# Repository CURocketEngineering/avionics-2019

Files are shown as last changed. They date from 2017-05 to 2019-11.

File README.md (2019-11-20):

## Deprecated
For more information, visit the [new, Python implementation](https://github.com/CURocketEngineering/avionics_main).

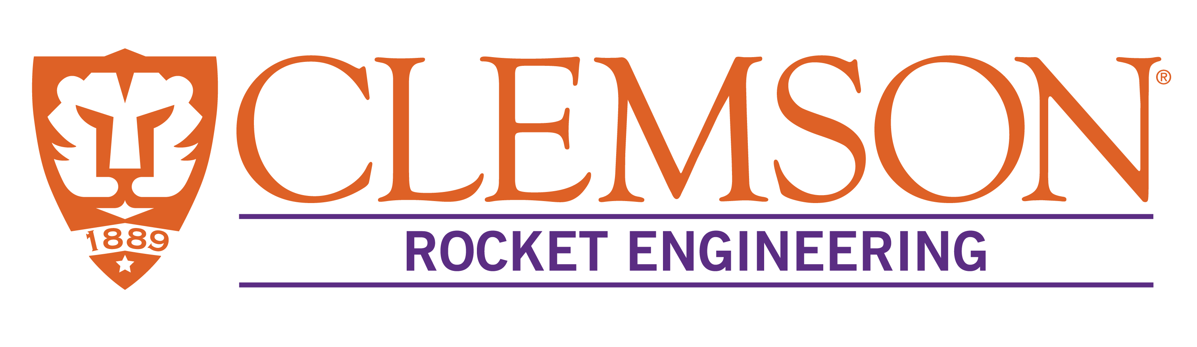
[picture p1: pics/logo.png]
CURocket Logo


### About
Clemson University Rocket Engineering (CURE) Avionics subteam program files. 
Powers CURE's competitive and non-competitive rockets. Used in the 
Intercollegiate Rocket Engineering Competition. Begun by Foster McLane, 2016.

### Documentation
* [`base/`](base/)
  * Code ran on the CURE base station for communication and telemetry
  * `main.py` for basic communication
  * `mpl.py` for graphical interpretation
  * `mpl_simulator.py` for simulating graphical interpretation
* [`cad/`](/cad)
  * Files for electrically engineering components in `eagle`
* [`data/`](data/)
  * Flight data
  * `jsongrapher.py` for ensuring simulation (and actual) data 
  * ['Complete simulation'](data/sim_data_graphed) for pictures of complete simulations
* [`extra/`](extra/)
  * Testing
  * GPS and XBEE `.ino` files
* [`main/`](main/)
  * Code ran on CURE rockets used for data collection, state changes, and telemetry
* [`pics/`](pics/)
  * Pictures used in this github
* [`xbee/bypass/`](xbee/bypass/)
  * Communication

### License
This project is licensed used the GNU General Public License v3.0

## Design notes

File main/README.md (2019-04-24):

# On-board avionics
### Usage
#### Compiling and Running
1. `make` to compile and run
#### Debugging
1. *todo*
#### Configuration
Configuration for several parameters can be made via `config.h`.

### Components
#### Current Components
* General Hardware
  * Teensy 3.5 Arduino
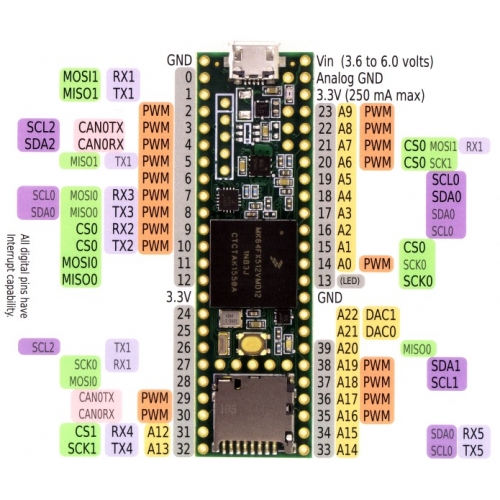
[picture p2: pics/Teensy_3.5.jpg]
Teensy
  * 
* Sensors
  1. 9DOF - 3D gyroscope, magnetometer, and accelerometer
     * [sparkfun link](https://www.sparkfun.com/products/13944)
       * schematic and eagle files provided
     * I2C interface
  2. BME280 - altitude, pressure, and temperature
     * [sparkfun link](https://www.sparkfun.com/products/13676)
       * schematic and eagle files provided
     * 3.3V SPI interface and 5V tolerant I2C
     * 10 pins, < 6 used
  3. GPS 

### Wishlist
1. XBEE Voice Messages
2. Live video feed

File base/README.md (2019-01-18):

# Base Telemetry
### TODO
* Write `graph/` functions
  * speedometer
  * pitch, yaw, roll
* `mpl.py` aesthetic
* Where is command located in main?
* Command integration in mpl
* Camera?

### Running
#### Compiling and Running
1. `python2 main.py` for main telemetry
2. `python3 mpl.py` for visual data
   * Requires `main.py` to be running
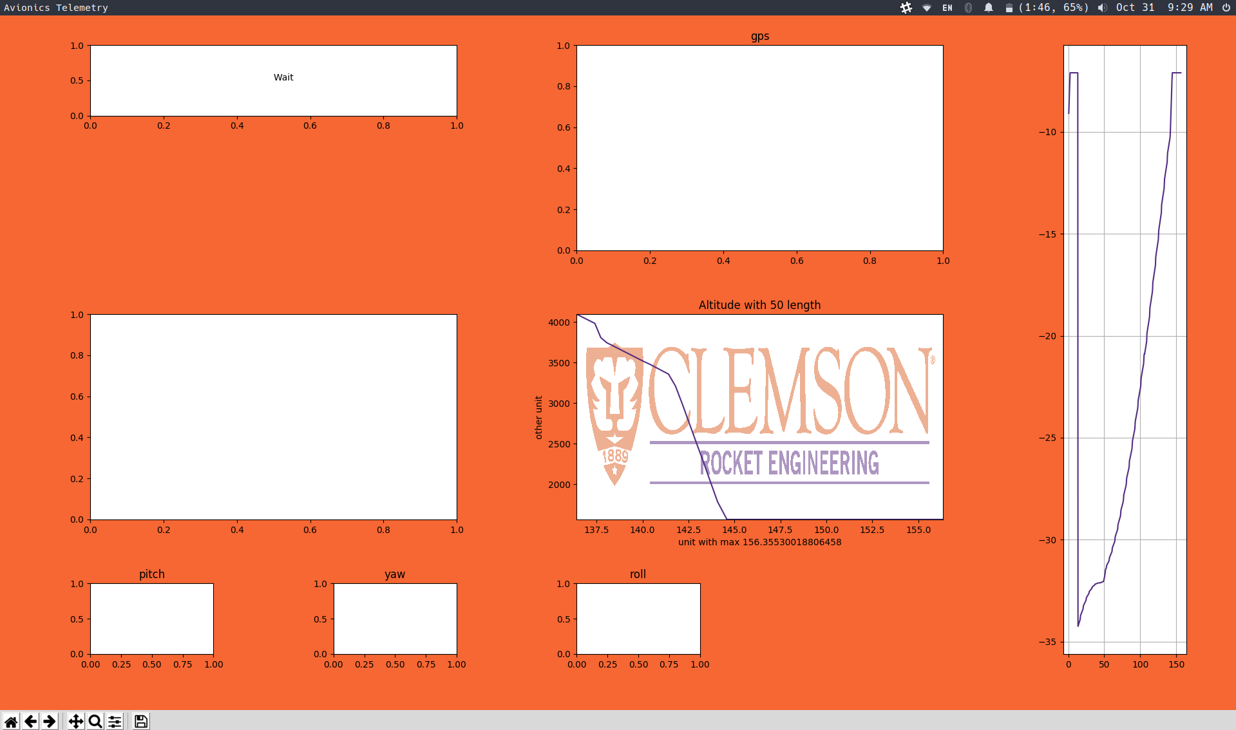
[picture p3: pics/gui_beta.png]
gui
   
#### Debugging
* To debug and test `mpl.py`
  1. Run `python3 mpl_simulator.py`
  2. Also run `python3 mpl.py` while the other is running
  3. Look at graphs and adjust program
* To debug and test `main.py`
  1. Pray to ~~the gods~~Foster that it works

### Information
* JSON Formatting
  * example: `{"sensors":{"gyro":{"x":0,"y":0,"z":0},"acc":{"x":0.000025,"y":0.000025,"z":38.01759},"mag":{"x":0,"y":0,"z":0},"att":{"r":6.451225e-7,"p":-6.451225e-7,"y":-0.108385},"bar":{"p":101324.9,"dp":0.890625,"alt":0.001904,"gnd":1237.593,"temp":0,"hum":0},"gps":{"lat":0,"lon":0,"hour":0,"min":0,"sec":0,"day":0,"mon":0,"year":0}},"type":"telemetry","time":804}`
  * Rocket will return self-contained json
    * Will always contain `type`, `time`, and `state`
      * `type` will be 1 of: state, telemetry, 
      * `time` is in units of (ms?)...
      * `state` will be 1 of the states: ignite, burn, apogee, wait, eject, fall, recover
    * Telemetry contains ... TODO

### Components
#### Current Components
* Communications Antenna
  * ???

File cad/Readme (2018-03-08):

Sparkfun Names of sensors (in eagle "add" component):
   1. Venus GPS ->                   GPS/ VENUS638FLPX-L
   2. Atmospheric Sensor Breakout -> Sensors/ BME280
   3. 9DoF Sensor Stick ->           Sensors/ LSM9DS1
   4. Antenna ->                     RF/ XBEE

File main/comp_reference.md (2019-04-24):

# Component Size Reference
### Summer 2019
| Component  | Length | Width | Iregular | Height |
| :--- | --- | --- | --- | --- |
| Teensy 3.6 | 2.5 in | 1.75 in | false | 1.3 in |
| 9Dof | 0.9 in | 0.25 in | false | |
| BME280 | 0.9 in | 0.5 in  | false | |
| | | | | |
| Antenna | 7 in | | diameter = 0.25 in | |

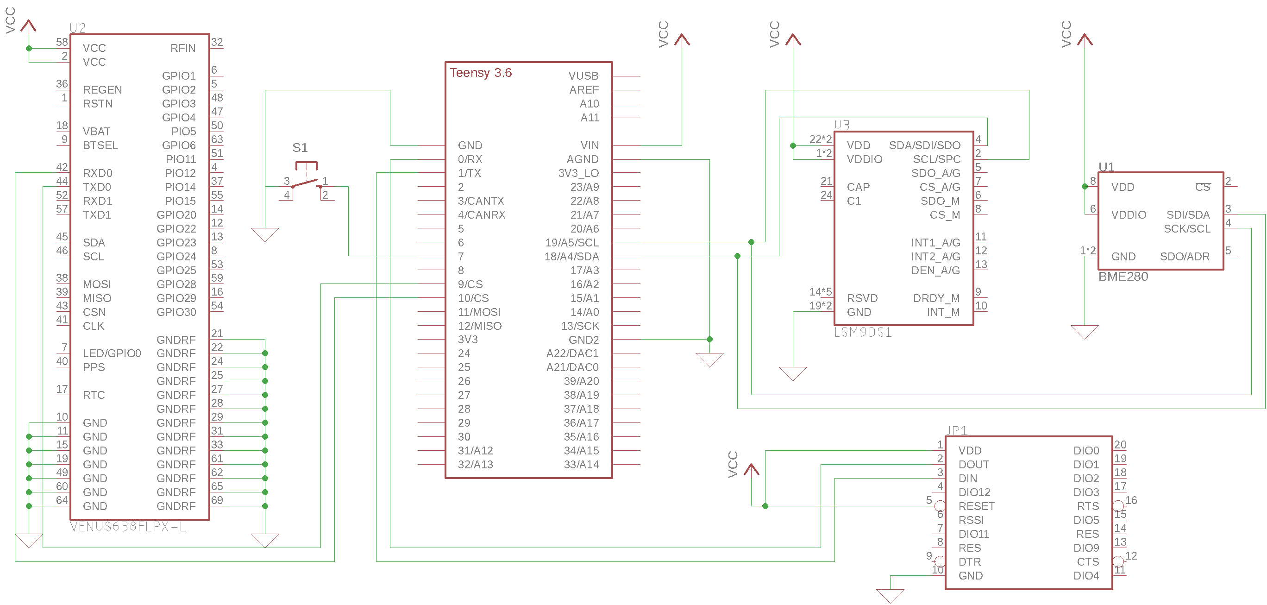
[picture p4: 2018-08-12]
cad/avionics-schematic.png

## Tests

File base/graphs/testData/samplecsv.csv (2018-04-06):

Time (sec) | Stage | Stage Time (sec) | Mach Number | Angle of Attack (deg) | CD | CL | Thrust (lb) | Weight (lb) | Drag (lb) | Lift (lb) | CG (in) | CP (in) | Stability Margin (cal) | Accel (ft/sec^2) | Accel-V (ft/sec^2) | Accel-H (ft/sec^2) | Velocity (ft/sec) | Vel-V (ft/sec) | Vel-H (ft/sec) | Pitch Attitude (deg) | Flight Path Angle (deg) | Altitude (ft) | Distance (ft) | Pressure (Pa)
0.010 | S | 0.010 | 0.010 | 0 | 0.5009655 | 0 | 152.8668 | 70 | 0 | 0 | 72.31744 | 79.27036 | 1.158819 | 38.0879567091562 | 38.0879567089588 | 0.000122630241795288 | 0.380879600001974 | 0.3808796 | 0.000001226302 | 89.9999 | 89.9999 | 0.001904398 | 0.00000000613151 | 101324.99
0.02 | S | 0.02 | 0.010 | 0 | 0.5009655 | 0 | 284.6732 | 69.99571 | 0.00001369519 | 0 | 72.30488 | 79.27036 | 1.160913 | 98.6779204506105 | 98.6779204503462 | 0.000228379674998849 | 1.3676590000045 | 1.367659 | 0.000003510099 | 89.9999 | 89.9999 | 0.01064709 | 0.00000002981351 | 101324.96
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

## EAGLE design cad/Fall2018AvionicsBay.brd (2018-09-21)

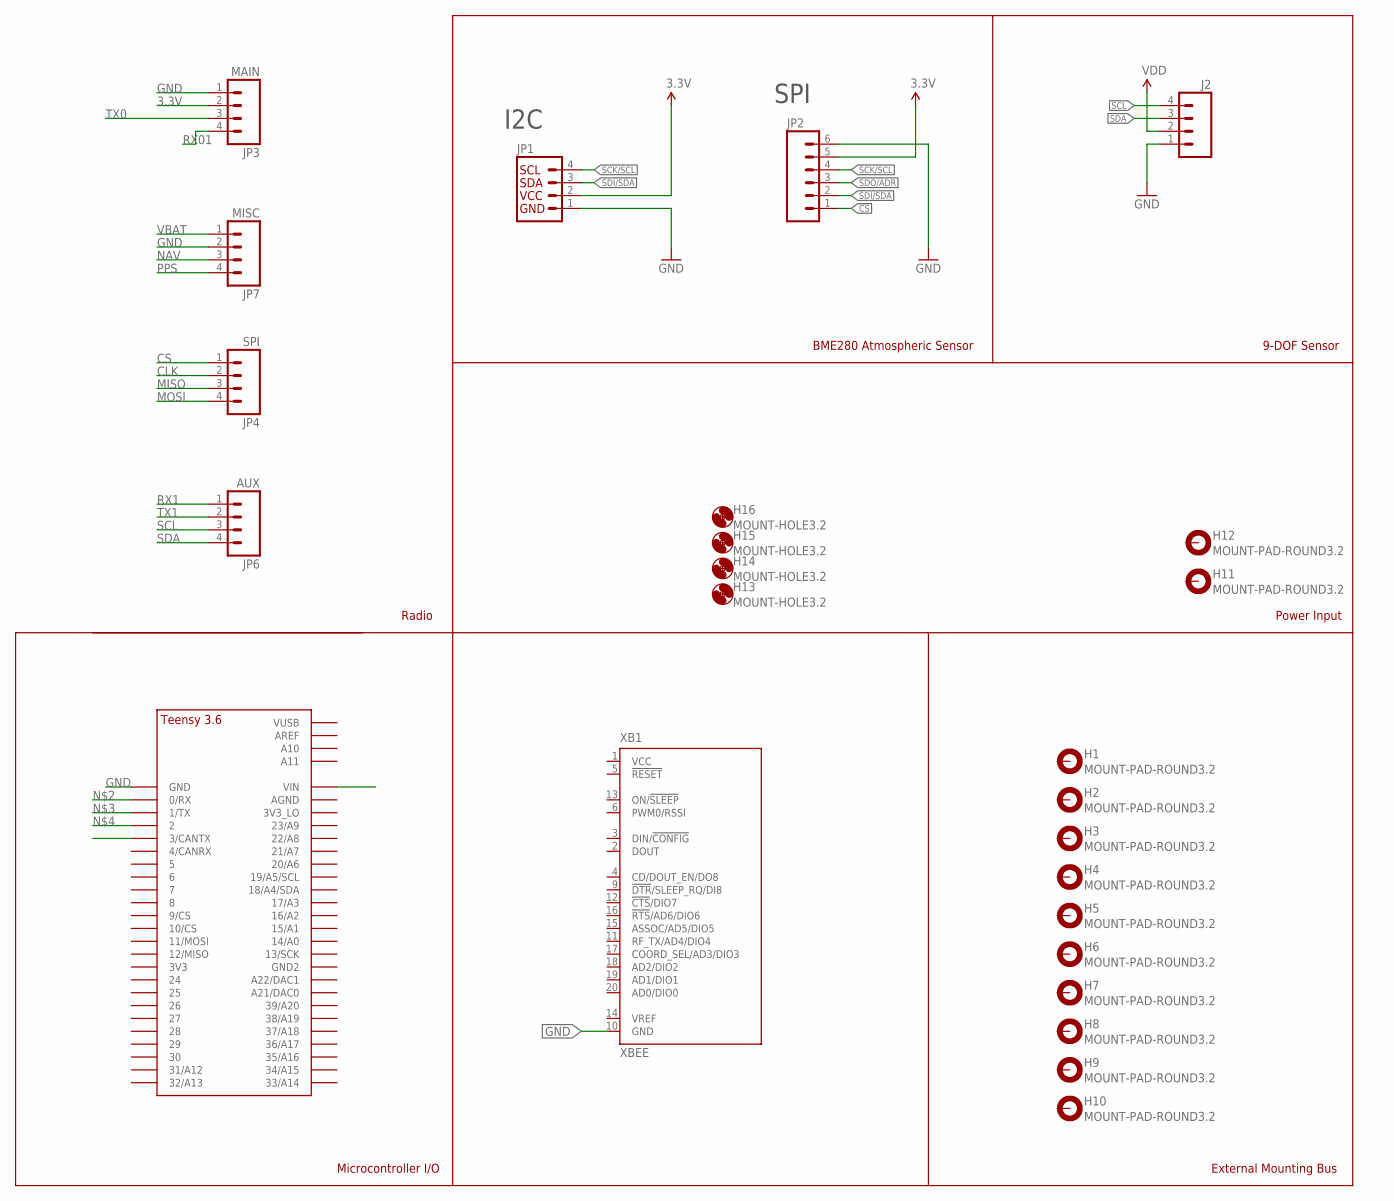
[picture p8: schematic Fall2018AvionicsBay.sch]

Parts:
H1, H2, H3, H4, H5, H6, H7, H8, H9, H10, H11, H12: MOUNT-PAD-ROUND3.2; 3,2-PAD
H13, H14, H15, H16: MOUNT-HOLE3.2; 3,2
J2: M04NO_SILK_ALL_ROUND; 1X04_NO_SILK_ALL_ROUND
JP1: I2C_STANDARD_NO_SILK; 1X04_NO_SILK
JP2: M06NO_SILK_FEMALE_PTH; 1X06_NO_SILK
JP3: MAIN; 1X04
JP4: SPI; 1X04
JP6: AUX; 1X04
JP7: MISC; 1X04
U$1: TEENSY_3.5/3.6_BASIC
XB1: XBEE

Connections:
3.3V: JP1.2, JP2.5, JP3.2
!CS: JP2.1
CLK: JP4.2
CS: JP4.1
GND: J2.1, JP1.1, JP2.6, JP3.1, JP7.2, U$1.GND, XB1.10 (GND)
MISO: JP4.3
MOSI: JP4.4
NAV: JP7.3
PPS: JP7.4
RX1: JP6.1
RX01: JP3.4
SCK/SCL: JP1.4, JP2.4
SCL: J2.4, JP6.3
SDA: J2.3, JP6.4
SDI/SDA: JP1.3, JP2.2
SDO/ADR: JP2.3
TX0: JP3.3
TX1: JP6.2
VBAT: JP7.1
VCC: XB1.1 (VCC)
VDD: J2.2

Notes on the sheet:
Microcontroller I/O
Radio
9-DOF Sensor
I2C
SPI
BME280 Atmospheric Sensor
External Mounting Bus
Power Input

Board: 2 copper layers, 25 parts (4 on the bottom side), 6 nets, no tracks yet.

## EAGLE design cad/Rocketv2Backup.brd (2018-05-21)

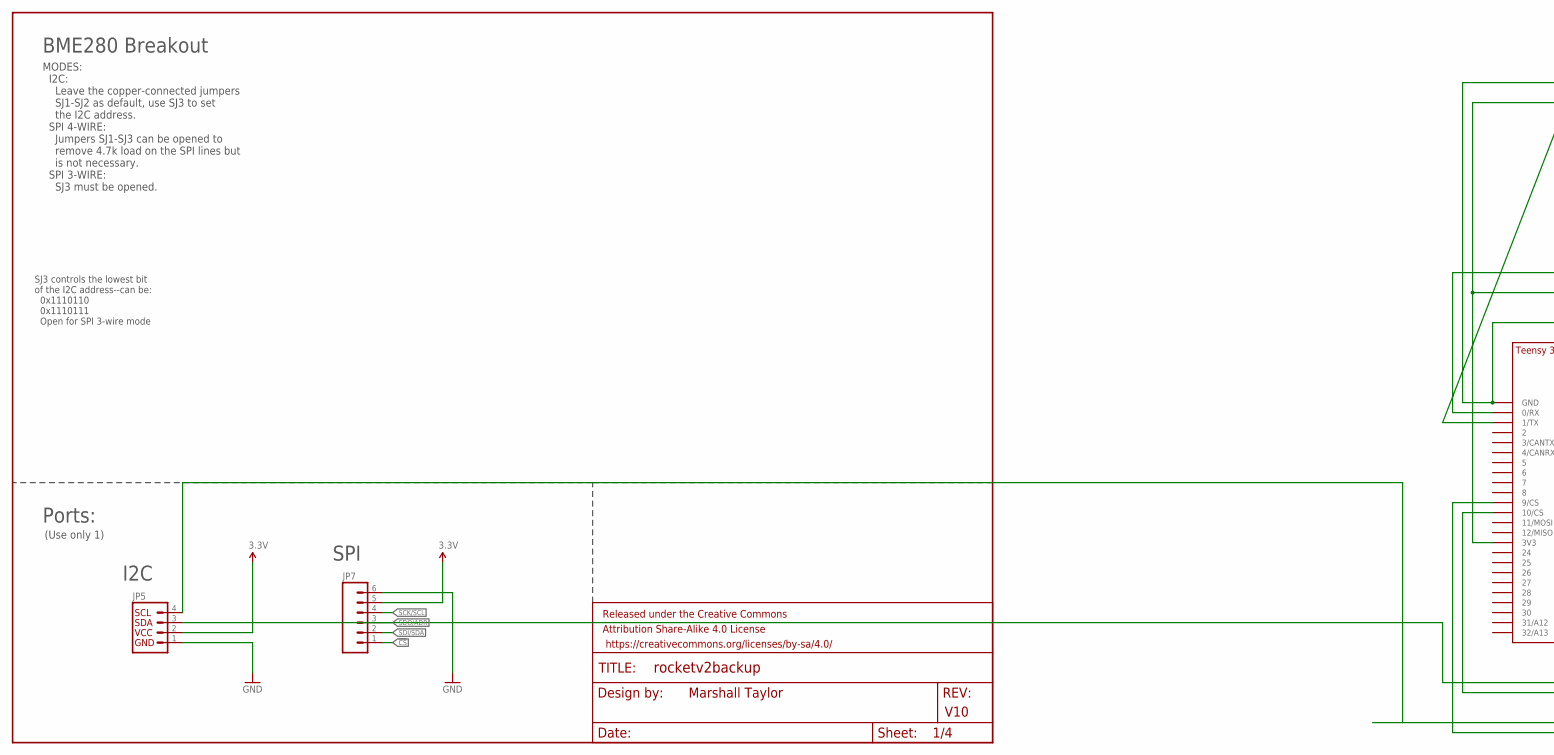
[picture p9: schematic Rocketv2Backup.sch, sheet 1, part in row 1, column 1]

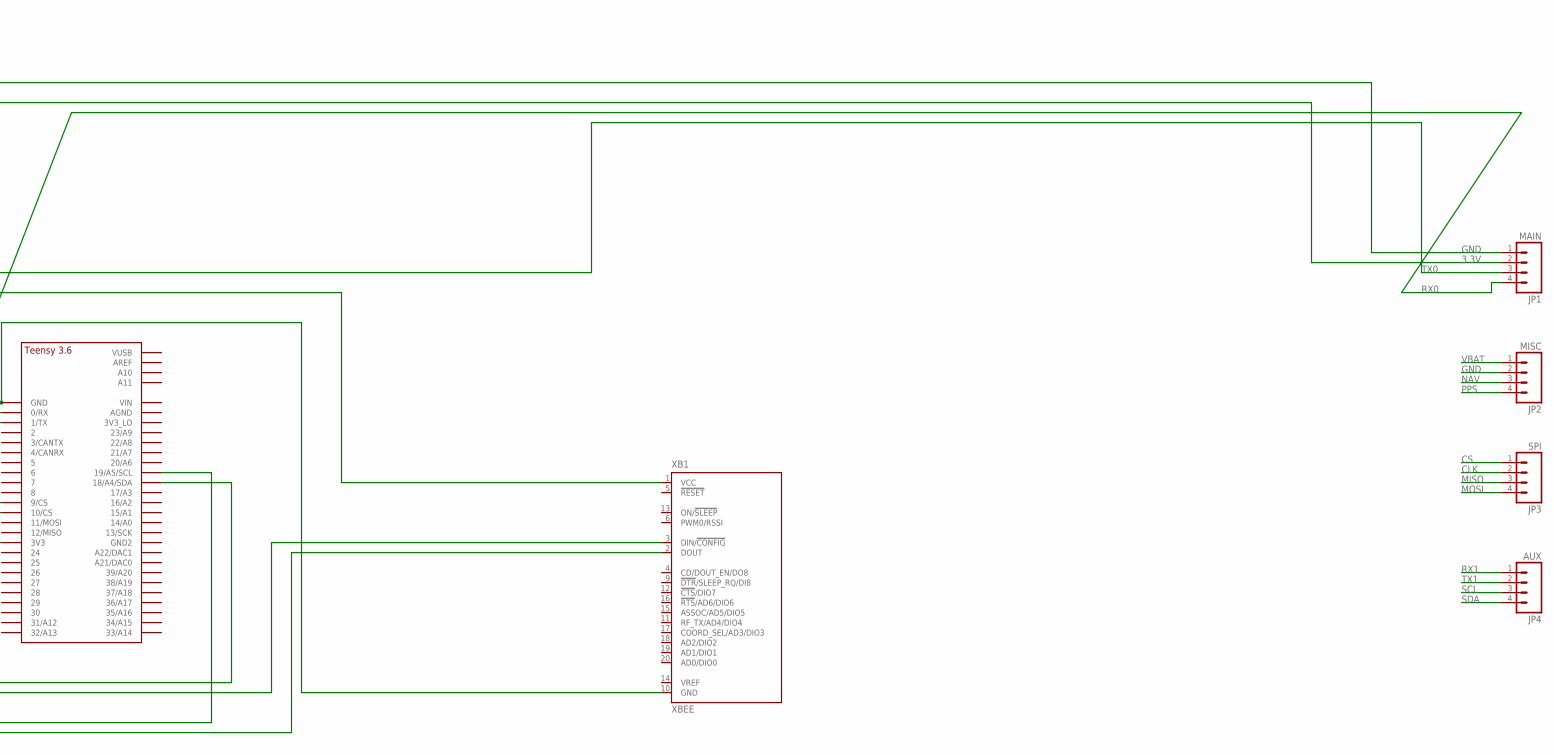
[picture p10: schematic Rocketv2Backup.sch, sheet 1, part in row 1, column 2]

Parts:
FRAME3: FRAME-LETTER; CREATIVE_COMMONS
JP1: MAIN; 1X04
JP2: MISC; 1X04
JP3: SPI; 1X04
JP4: AUX; 1X04
JP5: I2C_STANDARD_NO_SILK; 1X04_NO_SILK
JP7: M06NO_SILK_FEMALE_PTH; 1X06_NO_SILK
U$1: TEENSY_3.5/3.6_BASIC
XB1: XBEE

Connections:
3.3V: JP1.2, JP5.2, JP7.5, U$1.3V3, XB1.1 (VCC)
!CS: JP7.1
CLK: JP3.2
CS: JP3.1
GND: JP1.1, JP2.2, JP5.1, JP7.6, U$1.GND, XB1.10 (GND); also elsewhere on the board
MISO: JP3.3
MOSI: JP3.4
unnamed: JP5.4, U$1.19/A5/SCL
unnamed: U$1.10/CS, XB1.3 (DIN/!CONFIG)
unnamed: U$1.9/CS, XB1.2 (DOUT)
NAV: JP2.3
PPS: JP2.4
RX0: JP1.4, U$1.1/TX
RX1: JP4.1
SCK/SCL: JP7.4
SCL: JP4.3; also elsewhere on the board
SDA: JP4.4; also elsewhere on the board
SDI/SDA: JP5.3, JP7.2, U$1.18/A4/SDA
SDO/ADR: JP7.3
TX0: JP1.3, U$1.0/RX
TX1: JP4.2
VBAT: JP2.1

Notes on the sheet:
Marshall Taylor
V10
BME280 Breakout
SJ3 controls the lowest bit of the I2C address--can be: 0x1110110 0x1110111 Open for SPI 3-wire mode
Ports:
(Use only 1)
I2C
SPI
MODES: I2C: Leave the copper-connected jumpers SJ1-SJ2 as default, use SJ3 to set the I2C address. SPI 4-WIRE: Jumpers SJ1-SJ3 can be opened to remove 4.7k load on the SPI lines but is not necessary. SPI 3-WIRE: SJ3 must be opened.

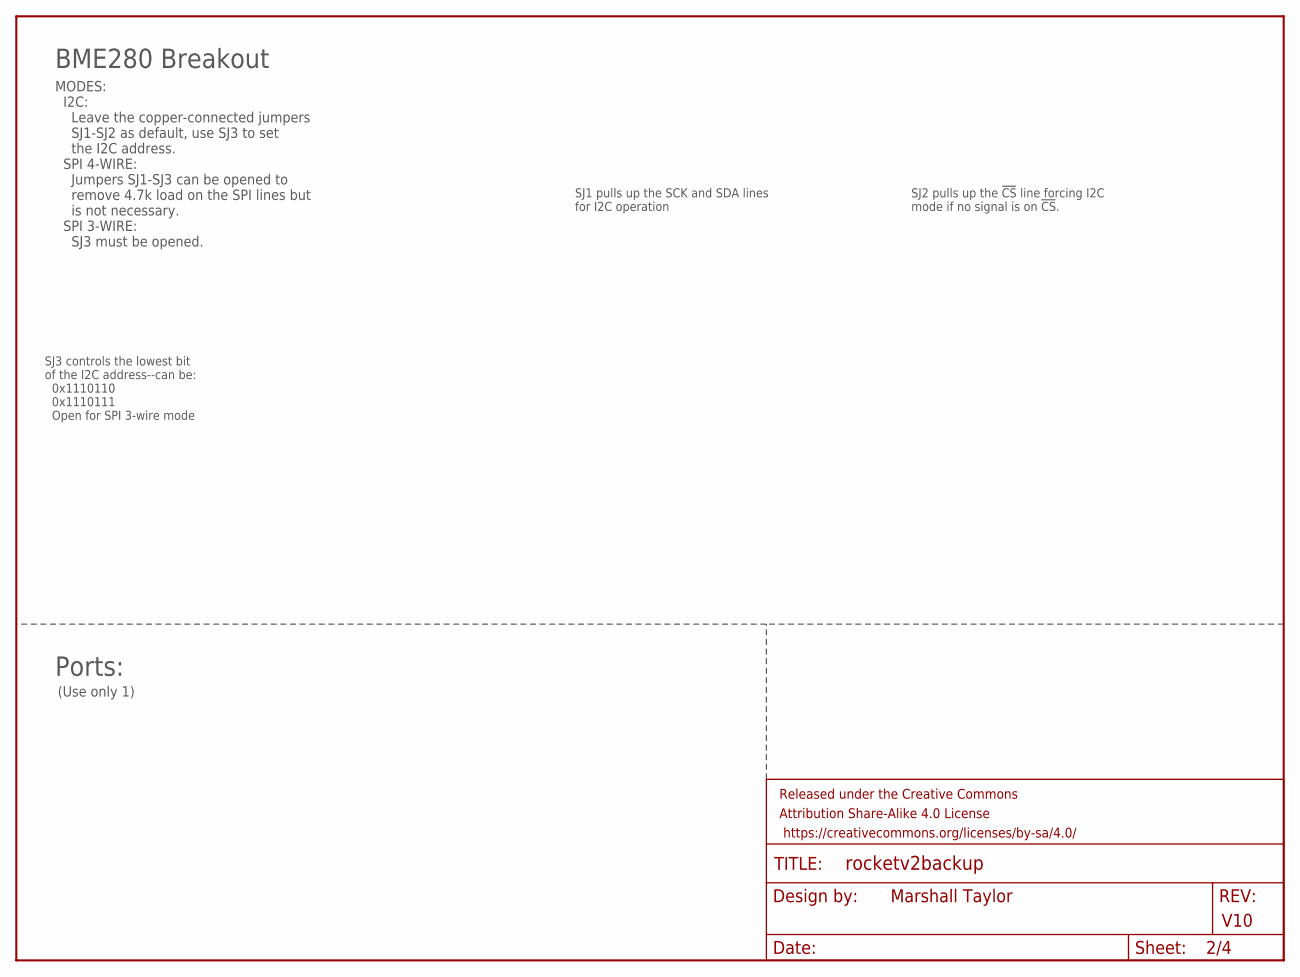
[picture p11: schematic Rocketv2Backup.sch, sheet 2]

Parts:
FRAME1: FRAME-LETTER; CREATIVE_COMMONS

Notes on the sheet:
Marshall Taylor
V10
BME280 Breakout
SJ3 controls the lowest bit of the I2C address--can be: 0x1110110 0x1110111 Open for SPI 3-wire mode
SJ1 pulls up the SCK and SDA lines for I2C operation
Ports:
(Use only 1)
MODES: I2C: Leave the copper-connected jumpers SJ1-SJ2 as default, use SJ3 to set the I2C address. SPI 4-WIRE: Jumpers SJ1-SJ3 can be opened to remove 4.7k load on the SPI lines but is not necessary. SPI 3-WIRE: SJ3 must be opened.
SJ2 pulls up the !CS! line forcing I2C mode if no signal is on !CS!.

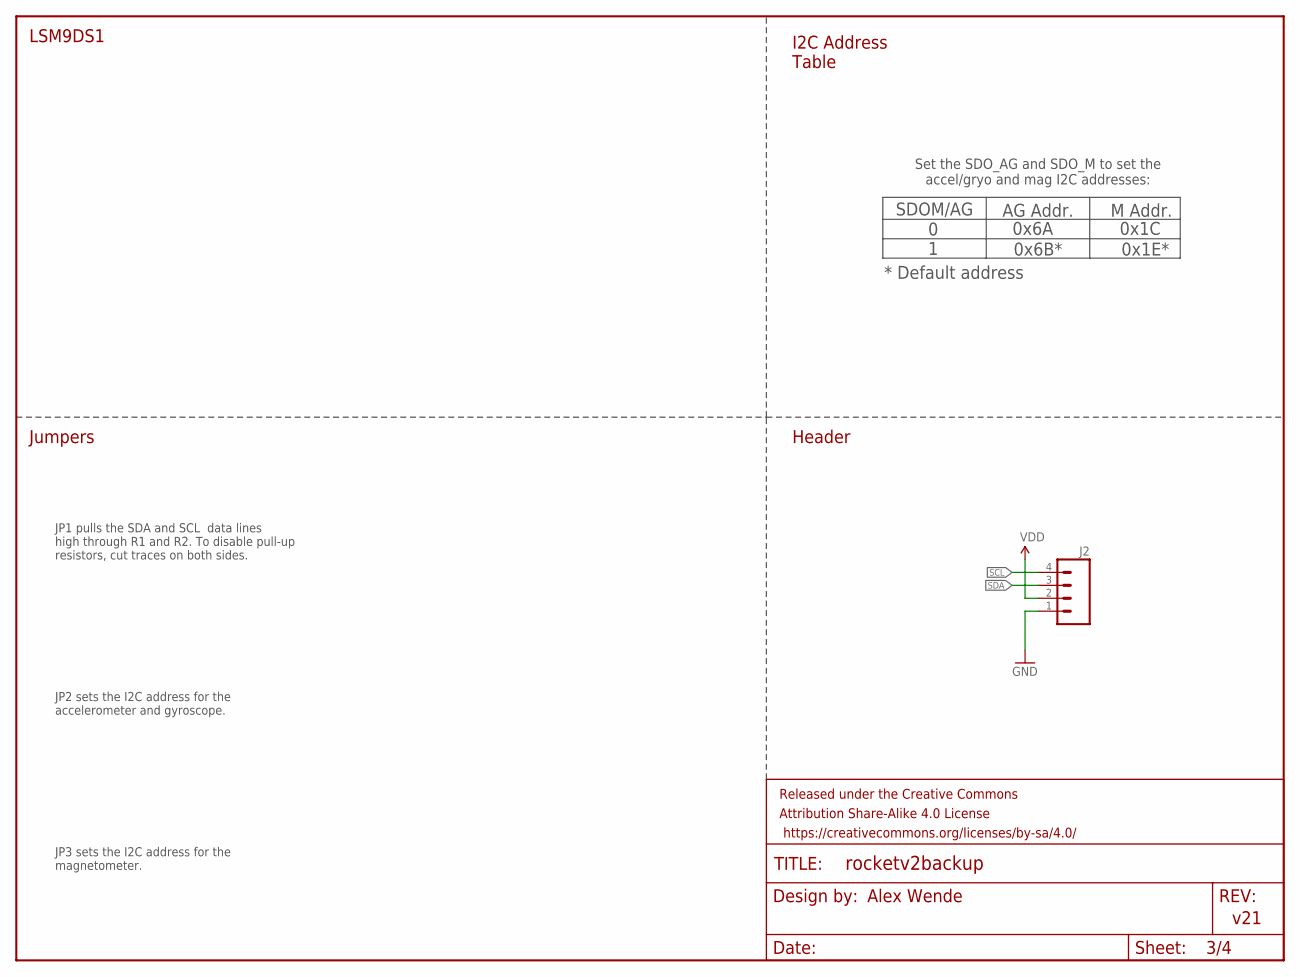
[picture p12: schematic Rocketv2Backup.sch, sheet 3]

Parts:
FRAME2: FRAME-LETTER; CREATIVE_COMMONS
J2: M04NO_SILK_ALL_ROUND; 1X04_NO_SILK_ALL_ROUND

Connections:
GND: J2.1; also elsewhere on the board
SCL: J2.4; also elsewhere on the board
SDA: J2.3; also elsewhere on the board
VDD: J2.2

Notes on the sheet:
Alex Wende
v21
LSM9DS1
SDOM/AG
AG Addr.
0 1
M Addr.
Set the SDO_AG and SDO_M to set the accel/gryo and mag I2C addresses:
I2C Address Table
Header
Jumpers
JP1 pulls the SDA and SCL data lines high through R1 and R2. To disable pull-up resistors, cut traces on both sides.
JP2 sets the I2C address for the accelerometer and gyroscope.
JP3 sets the I2C address for the magnetometer.
0x6A
0x6B*
0x1C
0x1E*
* Default address

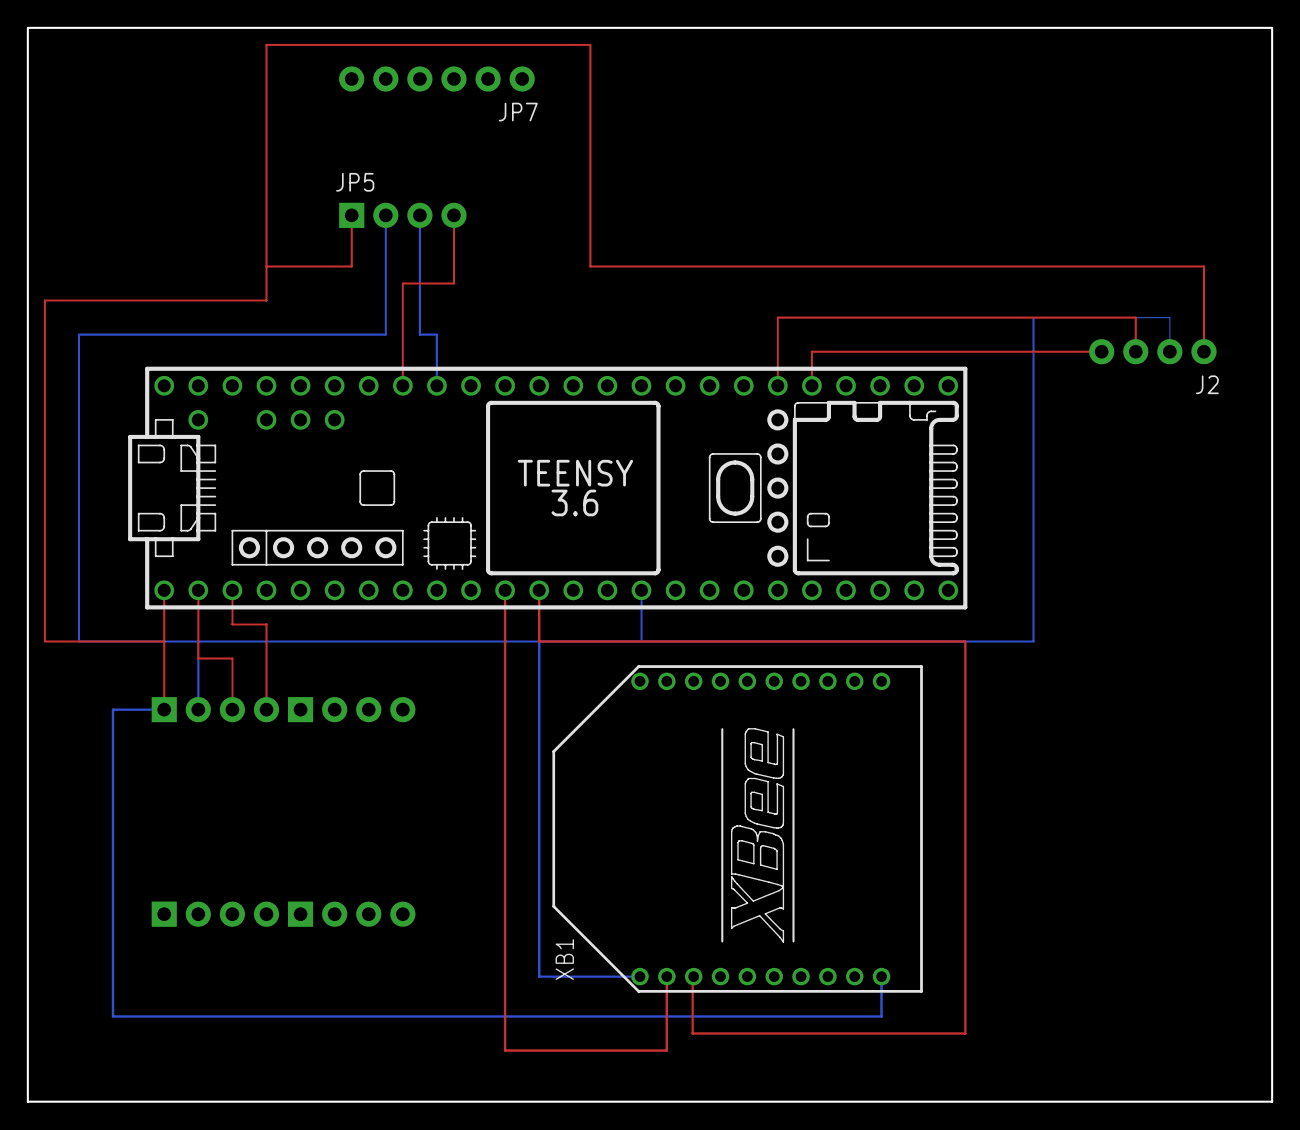
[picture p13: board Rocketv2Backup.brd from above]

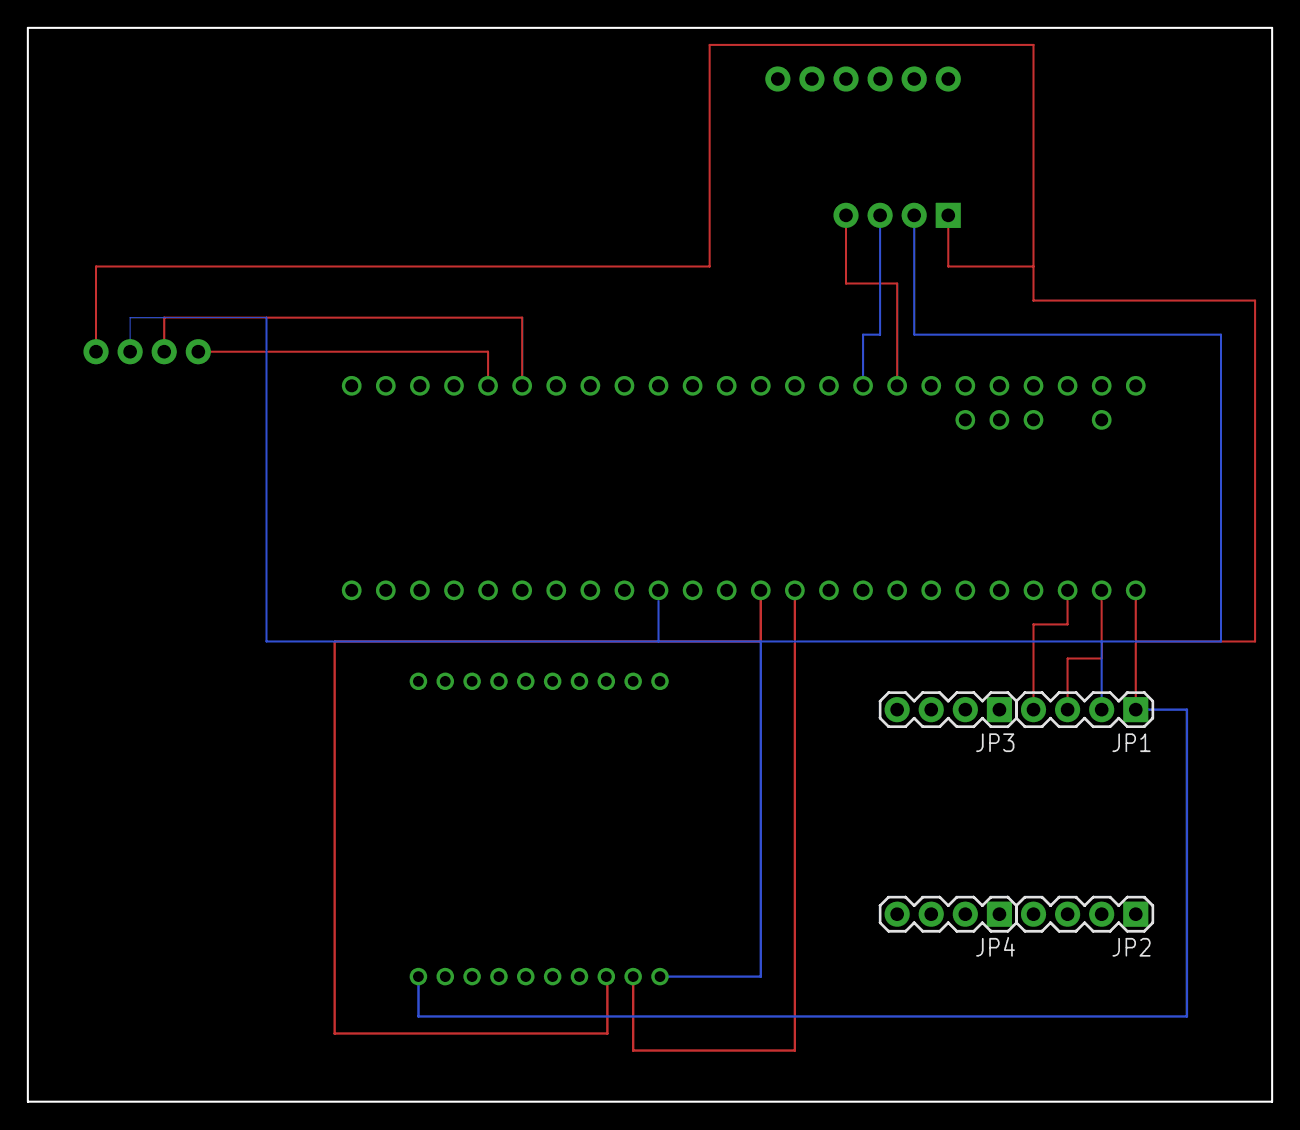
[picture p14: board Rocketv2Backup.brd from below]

Board: 2 copper layers, 92.7 x 80.0 mm, 12 parts (4 on the bottom side), 10 nets.

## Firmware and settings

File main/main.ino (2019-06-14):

/*
 * Main v0.5
 *
 * Main computer logic handling: button inputs, debug outputs, sensor inputs,
 * ignition, parachute evjection, and telemetry. Telemetry and commands are
 * communicated with the base station over the radios on a best effort basis.
 * Everything else is a critical function.
 */

/* DEFINITIONS */

// Initialization of sensor data
#define SENSOR_INIT 20
#define SENSOR_DELAY 10

/* LIBRARIES */
#include "debug.h"
#include "ninedof.h"
#include "state.h"
#include "barometer.h"
#include "datalog.h"
#include "communication.h"
#include "gps.h"
#include <EEPROM.h>

/* MAIN PROGRAM FUNCTIONS */
void setup() {
    // Clear EEPROM REMOVE TODO
    for (int i = 0 ; i < EEPROM.length() ; i++) {
      EEPROM.write(i, 0);
    }
  
    // Initialize debug leds
    debug_init();

    // Initialize communication with the ninedof sensor
    ninedof_init();

    // Initialize communication with the barometer
    barometer_init();

    // Initialize communication with GPS receiver
    gps_init();

    // Initialize blackbox datalogger
    datalog_init();

    // Initialize communication with the base station
    communication_init();

    // Define initial state
    state = INIT;
    debug = 0b0000000000000000;

    // Initialize sensor data
    gyro.x = gyro.y = gyro.z = 0;
    acc.x = acc.y = acc.z = 0;
    mag.x = mag.y = mag.z = 0;

    bar.p = 808;
    bar.dp = 0;

    bar.alt = 0;
    bar.gnd = 0;

    bar.temp = 0;
    bar.hum = 0;

    // Sample filter seed data
    unsigned long gyro_x = 0, gyro_y = 0, gyro_z = 0;
    unsigned long acc_x = 0, acc_y = 0, acc_z = 0;
    unsigned long mag_x = 0, mag_y = 0, mag_z = 0;
    unsigned long bar_p = 0, bar_dp = 0;
    unsigned long bar_alt = 0;
    unsigned long bar_temp = 0, bar_hum = 0;

    for (byte cnt = 0; cnt < SENSOR_INIT; cnt++) {
        ninedof_read(false);

        gyro_x += gyro.x;
        gyro_y += gyro.y;
        gyro_z += gyro.z;

        acc_x += acc.x;
        acc_y += acc.y;
        acc_z += acc.z;

        mag_x += mag.x;
        mag_y += mag.y;
        mag_z += mag.z;

        barometer_read(false);

        bar_p += bar.p;
        bar_dp += bar.dp;

        bar_alt += bar.alt;

        bar_temp += bar.temp;
        bar_hum += bar.hum;

        delay(SENSOR_DELAY);
    }

    gyro.x = gyro_x/SENSOR_INIT;
    gyro.y = gyro_y/SENSOR_INIT;
    gyro.z = gyro_z/SENSOR_INIT;

    acc.x = acc_x/SENSOR_INIT;
    acc.y = acc_y/SENSOR_INIT;
    acc.z = acc_z/SENSOR_INIT;

    mag.x = mag_x/SENSOR_INIT;
    mag.y = mag_y/SENSOR_INIT;
    mag.z = mag_z/SENSOR_INIT;

    bar.p = bar_p/SENSOR_INIT;
    bar.dp = bar_dp/SENSOR_INIT;

    bar.alt = bar_alt/SENSOR_INIT;

    bar.temp = bar_temp/SENSOR_INIT;
    bar.hum = bar_hum/SENSOR_INIT;

    gps_read();

    state_init();
}

void loop() {
    state_loop();
}

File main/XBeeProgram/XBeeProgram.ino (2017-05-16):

/*
 * XBeeProgram v0.1
 *
 * A program to allow one to communicate with the XBee over the Arduino's
 * serial line. This is generally used to modify the XBee using Digi's
 * software.
 */

#include <SoftwareSerial.h>

// note: these are the opposite of what is on the dev board
#define XBEE_RX 10
#define XBEE_TX 11

SoftwareSerial xbee(XBEE_RX, XBEE_TX);

void setup() {
  pinMode(XBEE_RX, INPUT);
  pinMode(XBEE_TX, OUTPUT);

  Serial.begin(9600);
  xbee.begin(9600);
}

void loop() {
  if (Serial.available())
    xbee.write(Serial.read());

  if (xbee.available())
    Serial.write(xbee.read());
}

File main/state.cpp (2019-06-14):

/*
 * Definition file for state functions
 */

/* LIBRARIES */
#include <avr/sleep.h>
#include <Arduino.h>
#include <EEPROM.h>
#include "Wire.h"
#include "state.h"
#include "communication.h"
#include "sim.h"
#include "debug.h"
#include "pins.h"
#include "config.h"

const char * states_arr[] = {
     "init",
     "idle",
     "halt",
     "test",
     "arm",
     "ignite",
     "burn",
     "coast",
     "apogee",
     "wait",
     "eject",
     "fall",
     "recover"
};

const char ** states = states_arr;

enum state_e state, state_prev;

String eeprom_header = EEPROM_HEADER;
int eeprom_state = eeprom_header.length();
int eeprom_debug = eeprom_header.length() + sizeof(state);
int eeprom_ground = eeprom_header.length() + sizeof(state) + sizeof(debug);

void idle() {
    while (state == IDLE) {
        // Update base station state
        communication_sendState(IDLE);

        // Check on ctrl term
        if (digitalRead(CTRL) == LOW) {
            // Wait for debounce and intent
            delay(5000);

            // If button still held
            if (digitalRead(CTRL) == LOW) {
                state = ARM;

                // Wait for unpress
                while (digitalRead(CTRL) != HIGH)
                    delay(100);

                // Wait for debounce
                delay(500);

                // Skip remainder of processing
                break;
            }
        }

        // Receive base command
        switch (communication_recvCommand()) {
            // Do nothing if no command
            case CMD_NONE:
                // Debug 1 Green - idling
                bitClear(debug, 13);
                bitSet(debug, 14);
                break;
                // Run test
            case CMD_TEST:
                state = TEST;
                break;
                // Arm rocket
            case CMD_ARM:
                state = ARM;
                break;
                // No communication with base station
            case NO_COMM:
                // Debug 1 Red - no communication with base station
                bitSet(debug, 13);
                bitClear(debug, 14);
                break;
                // Halt program in invalid state
            default:
                state = HALT;
        }

        // Update debug lights
        debug_write();

        delay(IDLE_DELAY);
    }
}

void halt() {
    // Debug 1-4 Red - halt
    debug = 0b0010010010010000;
    debug_write();

    // Turn off all important lines
    digitalWrite(TERM_MAIN, LOW);
    digitalWrite(TERM_DROGUE, LOW);

    // Clear interrupts and put processor to sleep
    //cli();
    //sleep_enable();
    //sleep_cpu();

    state = IDLE;
}

void test() {
    // Debug 1 Blue - run test
    bitSet(debug, 15);
    debug_write();

    // Update base station state
    communication_sendState(TEST);

    enum command_e cmd;

    while ((cmd = communication_recvCommand()) == CMD_NONE) {
        communication_updateTelemetry();
    }

    if (cmd == CMD_PASS) {
        communication_sendResult(true);
        // Debug 2 Green - pass test
        bitSet(debug, 11);
    }
    else {
        communication_sendResult(false);
        // Debug 2 Red - fail test
        bitSet(debug, 10);
    }

    debug_write();

    // Wait for lights to be read
    delay(2000);

    // Turn off lights
    bitClear(debug, 10);
    bitClear(debug, 11);
    bitClear(debug, 15);
    debug_write();

    state = IDLE;
}

void arm() {
    // Arm Blue - armed
    bitSet(debug, 3);
    debug_write();

    communication_sendState(ARM);
    state = IGNITE;    //DEBUG TODDO REMOVE
    return;

    while (state == ARM) {
        // Update base station state
        communication_updateTelemetry();

        // Sample ground altitude
        bar.gnd = bar.alt;

        // Check on ctrl term
        if (digitalRead(CTRL) == LOW) {
            // Wait for debounce and intent
            delay(5000);

            // If button still held
            if (digitalRead(CTRL) == LOW) {
                state = IGNITE;

                // Wait for unpress
                while (digitalRead(CTRL) != HIGH) {
                    delay(100);
                }

                // Wait for debounce
                delay(500);

                // Skip remainder of processing
                break;
            }
        }

        // Receive base station command
        switch (communication_recvCommand()) {
            // Do nothing if no command
            case CMD_NONE:
            case CMD_ARM:
                break;

            // Disarm rocket
            case CMD_DISARM:
                bitClear(debug, 3);
                state = IDLE;
                break;

            // Ignite rocket
            case CMD_IGNITE:
                state = IGNITE;
                break;

            // No communication with base station
            case NO_COMM:
                // Revert to idle state
                state = IDLE;
                break;

            // Halt program in invalid state
            default:
                state = HALT;
        }
    }

}

void ignite() {
    // Debug 3 Red - igniting
    bitSet(debug, 7);
    debug_write();

    // Update base station state
    communication_sendState(IGNITE);

#ifdef SIM
    sim_start = millis();
#endif

    // Store ground in EEPROM
    EEPROM.put(eeprom_ground, bar.gnd);

    // Wait for rocket to move up
    communication_updateTelemetry();
    while (NINEDOF_UP < MIN_ACCEL) {
        communication_updateTelemetry();
    }

    // Change to burn
    state = BURN;
}

void burn() {
    // Debug 3 Yellow - burning
    bitSet(debug, 8);
    debug_write();

    // Update base station state
    communication_sendState(BURN);

    // Update telemetry during burn
    communication_updateTelemetry();
    while (NINEDOF_UP > THRUST_ACCEL) {
        communication_updateTelemetry();
    }

    // Change to coast
    state = COAST;
}

void coast() {
    // Debug 3 Blue - coasting
    bitClear(debug, 7);
    bitClear(debug, 8);
    bitSet(debug, 9);
    debug_write();

    // Update base station state
    communication_sendState(COAST);

    // Update telemetry during coast
    communication_updateTelemetry();
    while (bar.dp < APOGEE_DPRES){
        communication_updateTelemetry();
    }

    // Change to apogee
    state = APOGEE;
}

void apogee() {
    // Debug 3 Green - apogee
    bitClear(debug, 9);
    bitSet(debug, 8);
    debug_write();

    // Update base station state
    communication_sendState(APOGEE);

    // Wait for ejection delay
    if (PARACHUTE_WAIT) delay(PARACHUTE_WAIT);

    // Send parachute signal
    /* OLD
    digitalWrite(TERM_DROGUE, HIGH);
    delay(PARACHUTE_DELAY);
    digitalWrite(TERM_DROGUE, LOW);
    */
    // Qwiic
    toggleRelay(true,TOGGLE_RELAY_ONE);
    delay(PARACHUTE_DELAY);
    toggleRelay(false,TOGGLE_RELAY_ONE);
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

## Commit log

2017-03-02 add basic kicad project
    [avionics.kicad_pcb, avionics.sch]
2017-03-02 add wip schematic
    [avionics.sch]
2017-03-06 add more wip main schematic
    [avionics.kicad_pcb, avionics.sch, main.sch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]
2017-03-08 add completed panel schematic revision 1
    [panel.sch]
2017-03-08 add mostly complete main section
    [main.sch, panel.sch]
2017-03-08 finalize main section
    [main.sch]
2017-03-28 add preliminary boards
    [main.kicad_pcb, main.sch, panel.kicad_pcb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]
2017-04-18 update main board with more compact footprint
    [main.kicad_pcb, main.sch, panel.kicad_pcb]
2017-04-18 adjust regulator pad
    [main.kicad_pcb]
2017-04-25 add board outlines
    [main.kicad_pcb, panel.kicad_pcb]
2017-04-25 remove payload project
    [payload.sch]
2017-05-09 patch in arming LED and fix backwards power caps
    [main.kicad_pcb, main.sch, panel.kicad_pcb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]
2017-05-09 fill zone for main board
    [main.kicad_pcb]
2017-05-09 fix wiring of latch
    [main.kicad_pcb, main.sch]
2017-05-09 add pull-up resistor to reset pin
    [main.kicad_pcb, main.sch]
2017-05-09 move cad files to cad folder and add skeleton source code
    [main.kicad_pcb, main.sch, panel.kicad_pcb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]
2017-05-10 force initial button state and fix crystal pins
    [main.kicad_pcb, main.sch, panel.kicad_pcb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]
2017-05-10 reconnect accelerometer to adc pins
    [main.kicad_pcb, main.sch]
2017-05-10 swap ready and reset buttons
    [main.kicad_pcb, main.sch, panel.kicad_pcb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]
2017-05-11 add more misc board fixes
    [main.kicad_pcb, main.sch, panel.kicad_pcb]
2017-05-15 add sample flight data file
    [flight.csv]
2017-05-16 moving main board information out of the way
    [main.kicad_pcb]
2017-05-16 adjust which values are silkscreened
    [main.kicad_pcb, panel.kicad_pcb]
2017-05-16 add mounting holes
    [main.kicad_pcb, panel.kicad_pcb]
2017-05-16 fix accelerometer connection
    [main.kicad_pcb, main.sch, panel.kicad_pcb]
2017-05-16 add code to measure accelerometer and barometer data
2017-06-01 break up fall phase and make all LEDs being green meaning successful recovery
2017-06-09 fix unconnected GND net in panel
    [panel.kicad_pcb, panel.sch]
2017-06-09 add pressure to flight data
    [flight.csv]
2017-06-09 add debug mode which reads sensors from serial
2017-06-09 add test program which simulates sensor values and payload
2017-06-09 fill out pin numbers and allow programming with usbtiny
2017-06-10 change LEDs to command anode and release rev 3
    [main.kicad_pcb, main.sch, panel.kicad_pcb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]
2017-06-10 add support for continuing flight even if main computer resets
    [Test.ino]
2017-06-10 add automatic board detection based on directory
2017-06-10 fix port numbers and save debug LEDs in EEPROM
2017-06-11 add diode after flop and start hand-made traces
    [main.kicad_pcb, main.sch, panel.kicad_pcb]
2017-06-11 change board back to uno until we have 8MHz crystal/resonator
2017-06-11 fix LED output and store ground in EEPROM
2017-06-12 fix backwards MOSFETs
    [main.kicad_pcb, main.sch]
2017-06-16 update programming for circuit board
2017-06-20 move to revision 4 of boards
    [avionics.kicad_pcb, avionics.sch, main.kicad_pcb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]
2017-06-20 add LED test
2017-06-20 fix edge cuts on panel
    [panel.kicad_pcb]
2017-06-20 rename debug to radio header
    [main.kicad_pcb, main.sch]
2017-06-21 rename payload time to timing to avoid name clash
    [main.py]
2017-06-22 switch payload communication to UART instead of I²C
2017-06-22 update kicad project files
2017-06-22 add payload sensor data and communication
2017-06-22 remove remaining references to Wire
2017-06-22 fix uarts and disable missing sensors
    [comm.py]
2017-06-22 disable magnetometer too
2017-06-22 print data transfered
2017-06-22 fix radio uart
2017-06-23 add payload arduino GPS code
2017-06-23 use i2c correctly in gps
2017-06-23 fix error in test program
    [Test.ino]
2017-06-24 make small misc payload fixes
    [comm.py]
2017-10-12 Remove wire protocol in GPS program
2017-10-13 change board definition for Main
2017-11-08 fix small pointless kicad issue
    [main.sch]
2017-11-15 remove cad files
    [avionics.kicad_pcb, avionics.sch, main.kicad_pcb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]
2017-11-29 Split main_v0.2
    Split apart the initial main v0.2 file into main.ino and various .h/.cpp files. Compiles correctly on (Windows) Arduino IDE and PlatformIO (Atom package).
    [communication.cpp]
2018-01-23 Initial 9DoF sensor calculations
    This is not integrated at all with the rest of the /main files. This is a preliminary idea as to how the 9DoF sensor may be implemented in the future. Deviation calculations use the gyroscope's X and Z axes (and if deviations in rotational velocity occur), which may be the wrong way to calculate if the rocket deviates.
    Uses Arduino's Serial.print to display data in the Serial Monitor (usually located in the Arduino IDE; not sure if Linux is able to view this).
    The programs should theoretically work, but no testing has been done.
    Requires the SparkFunLSM9DS1.h library (located https://github.com/sparkfun/SparkFun_LSM9DS1_Arduino_Library).
2018-02-15 update automatically finding the Arduino dir in macOS
2018-02-15 Create Schematics and Data Sheets
2018-03-06 add GPS date/time and add compilation fixes
    [communication.cpp]
2018-03-06 rename Datasheets and Schematics to cad
    [McCloud Schematic.sch, McCloud9.sch]
2018-03-06 clean up cad a little
    [McCloud9.sch]
2018-03-14 fix little issues in communication.cpp
    [communication.cpp]
2018-03-15 update cad for combined i2c
    [McCloud9.sch]
2018-03-15 ignore backup cad files
2018-03-16 fix python syntax error
    [main.py]
2018-03-18 print a newline to serial after message
2018-03-24 add attitude to sensor output
2018-03-24 fix issue with same data across 9dof sensor
    [communication.cpp]
2018-03-28 trying threading lol
2018-03-28 added fake data and created accompanying function
    [flight.csv]
2018-03-28 add control switch
    [McCloud9.sch]
2018-04-11 Removed comm.init(), must wait to show fake data if error.
    [mpl.py]
2018-04-19 color fix for comm graphs
    [mpl.py]
2018-05-21 Added Board and Schematic files
    [Rocketv2Backup.brd, Rocketv2Backup.sch]
2018-06-13 move cad files
    [Rocketv2Backup.brd, Rocketv2Backup.sch]
2018-06-18 remove pin collision
2018-06-23 create teensy makefile
2018-06-23 add bypass src.uart
2018-06-23 remove bypass src.uart
2018-07-08 fix running make boards or make clean without setting speed
2018-09-21 license code under GPLv3
    enacted by all developers of the current program 2018-09-21
2018-10-07 updated readme and moved eagle files
    [Fall2018AvionicsBay.brd, Fall2018AvionicsBay.sch]
2018-10-07 moved files
    [Fall2018AvionicsBay.brd, Fall2018AvionicsBay.sch]
2018-10-10 documentation and begin fixing mpl.py
    [comm.py, mpl.py]
2018-10-29 Visual with quickbox
    [samplecsv.csv]
2018-10-30 bug fix and visual example
    [box.py, mpl.py]
2019-04-24 bug fix update readmes
    [box.py, main.py]
2019-05-29 fixed wire.h issue, and toggleRelay bug
    [state.cpp]

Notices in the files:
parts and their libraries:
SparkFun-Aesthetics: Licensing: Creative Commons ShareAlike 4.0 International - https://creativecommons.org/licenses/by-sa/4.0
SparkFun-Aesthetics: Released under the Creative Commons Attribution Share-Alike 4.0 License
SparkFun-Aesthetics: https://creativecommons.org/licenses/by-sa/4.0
